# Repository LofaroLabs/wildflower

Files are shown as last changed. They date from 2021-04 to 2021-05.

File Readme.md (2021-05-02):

<!DOCTYPE HTML>
<html lang="en-US">
  <head>
    <meta charset="UTF-8">
  </head>
  <body>
    <!--Main Header-->
    <h1> Project Wildflower UAS </h1>
    <!--Logos-->
    <p float="left">
      Lofaro Labs Logo
      Project Wildflower Logo
    </p>
    <!--Link Bar-->
    <div id="NavBar">
      <p>  
        <a href="#Introduction" target="_blank">Approach</a>
         | 
        <a href="#PCBAndPowerSystems" target="_blank">PCB & Power Systems</a>
         | 
        <a href="#SoftwareAndPsuedocode">Software & Psuedocode</a>
         | 
        <a href="#BriefHistoryofArduino">Brief History of Arduino</a>
         | 
        <a href="#SensorsAndMotorDrivers">Sensors & Motor Drivers</a>
         | 
        <a href="#Results">Results</a>
         | 
        <a href="#Conclusion">Conclusion</a>
         | 
        <a href="#References">References</a>
         | 
        <a href="#ProjectPresentation">Project Presentation</a>
         | 
        <a href="https://www.youtube.com/watch?v=GgbFuCZchfk" target="_blank">Project Presentation on YouTube</a>
         | 
        <a href="http://lofarolabs.com/" target="_blank">Lofaro Labs Website</a>
    </div>
    <!--Section 0: Abstract-->
    <div>
      <p> 
        &nbsp;&nbsp;&nbsp;&nbsp;Since the turn of the millennium, unmanned aerial vehicles (UAVs) have gone from being used for highly specialized applications to becoming one of the primary approaches to mission success within the defense sector. UAVs are unmatched in terms of mission success versus collateral damage - and as production costs continue to rapidly fall, it is only natural that UAVs will continue to become a more common tool of militaries around the world. One of the most recent developments in the world of UAVs has been the growing consumer market for ultralight unmanned aerial systems (UAS). Some commercial products have demonstrated the viability and flexibility of inexpensive, open source, ultralight UAS systems. Unfortunately, most consumer products on the market cannot be approved for high security applications due to the inherent security risks posed by foreign-manufactured products. Therefore, the defense industry has need of an American-made ultralight UAS if it wants to pursue the potential applications that this technology allows. 
      </p>
      <p>
        &nbsp;&nbsp;&nbsp;&nbsp;This paper entails the results of our research and development work over the past 9 months. We are proud to present the results of our testing on a brushed-motor, unmanned aerial system (UAS) quadcopter designed in preparation of developing a brushless quadcopter in the future. Beginning in September of 2020, we began to perform research on designing a lightweight quadcopter out of a single printed circuit board (PCB) in order to meet the need for a quality, domestically produced UAS. Today, a great number of quadcopters are produced in foreign countries or with foreign programmed components. While many of these common quadcopters have demonstrated the general usefulness and cost-efficiency of their use, their foreign origins make them unusable by the federal government and military sectors due to concerns over information safety. Data concerning their activities is often sent to and kept on insecure servers[CNN and OSTI.gov, second not quoted], and can provide easy access points for malicious entities to otherwise secure systems when allowed to connect[Avast]. 
      </p>
      <p>
        &nbsp;&nbsp;&nbsp;&nbsp; As a result, our project was designed to fill this gap by providing a secure, American made UAS capable of remote operations. This paper covers the design process, creation, and testing of our quadcopter over the past two semesters. Our section on the PCB & Power System Design describes the design choices we made in structuring our board, as well as our choice of using a dual power system to power the motors and microcontroller separately. The Software & Pseudocode section goes over the general flow of our real time system, and is followed by a Brief History of Arduino. Sensors and Motor Drivers describe the input and output devices we thought best fitting for our UAS. The control systems elaborates further on our real time system. Finally, the Unit Testing and Results slide show the results of our research as we make the Wildflower hover and tilt at will, bringing us to our conclusion.
      </p>
      <hr>
    </div>
    <!--Section 1: Introduction-->
    <div id="Introduction">
      <h1>Approach</h1>
      <h3>The Problem</h3>
      <p> 
        &nbsp;&nbsp;&nbsp;&nbsp;The idea for the Wildflower arose from the desire for an American designed and programmed quadcopter in a market saturated with foreign-made quadcopters. The need for American Unmanned Aerial Systems (UAS) has been apparent for several years. In August 2017, “the Army banned the use of DJI drones citing ‘cyber vulnerabilities’” [1,2]. In May 2018, the DoD followed suit, banning not only the purchase of DJI drones, but the purchase of all commercial off-the-shelf (COTS) drones” [3,4]. Shortly after, several alarming vulnerabilities were discovered involving the DJI Go Phone application [5]. Such vulnerabilities included “access to facial recognition data (even when the system was off)” [5]. It’s not a far stretch to assume that the ban on government funding for blacklisted drones may soon extend to universities that receive government grants.
      </p>
      <p>
        &nbsp;&nbsp;&nbsp;&nbsp;The COTS ban, while seemingly necessary, has left a lot of government employees and contractors with a job to do without the tools to do it. There have never been many US-made drones available on the market, but the pool of eligible candidates dwindles further when the drones containing foreign software are excluded. While there currently exists a number of American based alternatives for remote controlled unmanned aerial systems, such systems often cannot be used out-of-the-box for important security or government related tasks. For example, many of these UASs are not easily configurable, having been made for the general public to enjoy. Additionally, the communications methods for these systems might not be securable, posing a risk of malicious infiltration into crucial US government and military organizations. 
      </p>
      <h3>The Solution</h3>
      <p>
        &nbsp;&nbsp;&nbsp;&nbsp; Dr. Lofaro’s initial idea for the Wildflower was conceived as a direct result of his inability to use certain UAS’s for his work at the Naval Research Lab. Our project aims to fill this gap by providing a trustworthy and easily modifiable aerial system designed in a way that allows easy debugging and testing for those who use it. We make use of a VL6180x short-range light detection and ranging (LIDAR) sensor, a VL53L0x long-range LIDAR sensor, and a BNO055 inertial measurement unit (IMU) sensor to feed all of the information we need to our Adafruit Feather M0 microcontroller (MCU) with embedded ATWINC1500 Wifi chip, in order to keep it airborne and mobile. We communicate commands to the Feather over wi-fi and through a ground station that can be easily installed on a user’s computer, allowing for increased portability and relatively straightforward setup and teardown when moving from one area of use to another or starting to use it for the first time. 
      </p>
      <hr>
    </div>
    <!--Section 2: PCB & Power Systems-->
    <div id="PCBAndPowerSystems">
      <h1>PCB & Power Systems</h1>
      <div>
        <p> 
          &nbsp;&nbsp;&nbsp;&nbsp;The circuit board for the UAS design consists of a 51x51mm body with four 10mm arms connected to circular motor mounting points which are 19mm in diameter. The motors and rotors are mounted on the outer circle of the PCB connected to the quadrotor’s arms, while some of the heavier electronics are placed towards the center of the PCB for stability. 
        </p>
        <!--PCB-->
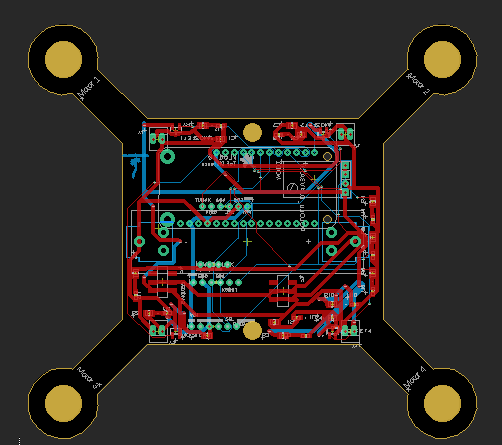
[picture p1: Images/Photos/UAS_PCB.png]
Final PCB
        
        <!--Schematic-->
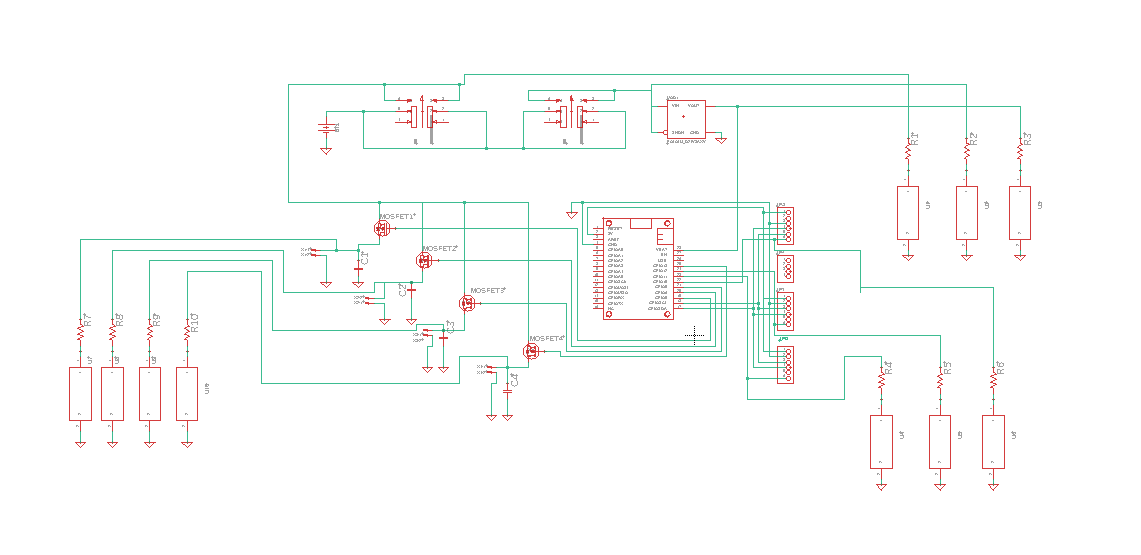
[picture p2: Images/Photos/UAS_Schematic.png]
Final Schematic
        
        <p>
          &nbsp;&nbsp;&nbsp;&nbsp;The UAS PCB circuitry consists of a battery to supply power to the circuit. Two switches are applied in parallel with the battery to function as on/off switches to the motors and the microcontroller respectively. From the on/off switch, power is supplied to the microcontroller through a 3.3V voltage regulator at 300milliamperes. This voltage regulator was chosen since the recommended voltage input to the Feather is 3 to 5 volts and the recommended current that is input to the Feather is 250 milliamperes to 400 milliamperes. The microcontroller then uses the 3.3-volt output pin to supply power to the close-range lidar sensor, the long-range lidar sensor, and the inertial measurement unit (IMU).  Power is supplied to the motors using a single metal-oxide-semiconductor field-effect transistor (MOSFET), rather than using an H-bridge circuit for simplicity. The power supplied from the battery is supplied to the drain terminal of the MOSFET and the source MOSFET is connected to the motors. The amount of power supplied to the motors is manipulated by pulse-width modulation of the gate terminal of the MOSFET. When applying a signal from the Feather to the MOSFET with a high duty cycle, the drain current will increase; however, the opposite will occur when the input signal has a low duty cycle. The drain current of a MOSFET acting in the saturation region can be calculated by the following equation:
        </p>
        <!--Drain Current Equation-->
        Drain Current Equation for MOSFET in the triode region
        <p>
          &nbsp;&nbsp;&nbsp;&nbsp;The transconductance parameter is the portion of this equation that dictates the amount of drain current based on the input voltage; thus, choosing a MOSFET with the correct transconductance parameter was critical. Another critical criterion that had to be met was having a low threshold voltage. With a low threshold voltage, the triode region of the MOSFET is entered with a low gate to source voltage. Since the gate to source voltage will at most be equivalent to the drain to source voltage in our case, the closest that our MOSFET will act to the triode region Is on the bound of the triode and saturation regions. For all of these reasons, we have chosen to use the SI2342DS. Shown below, this model of MOSFET will allow a large drain current to pass through MOSFET from the battery to the motor when a large gate voltage is applied; however, the opposite will occur when the gate to source voltage is lower than or equal to the threshold voltage. 
        </p>
        <!--Image of the FET graph-->
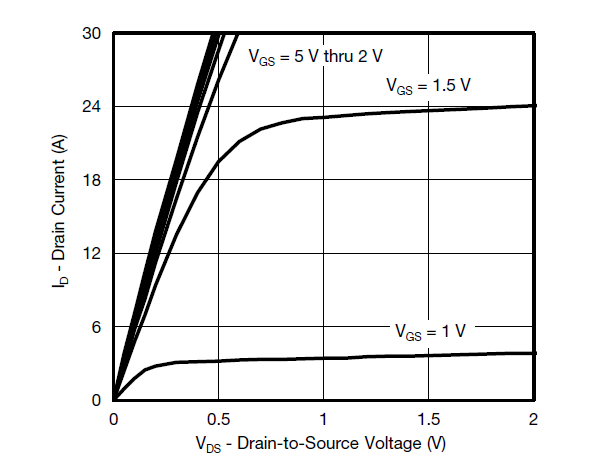
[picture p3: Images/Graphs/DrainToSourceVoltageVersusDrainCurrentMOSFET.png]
MOSFET Drain to Source Voltage Versus Drain Current
        
        <p>
          &nbsp;&nbsp;&nbsp;&nbsp;Finally, the node connected to the motor inputs is also connected to a decoupling capacitor. This capacitor will cancel out some of the impedance caused by the inductive load of the motor as well as filter out any high frequency signal components. 
        </p>
        <hr>
      </div>
    </div>
    <!--Section 3: Software and Psuedocode-->
    <div id="SoftwareAndPsuedocode">
      <h1>Software & Psuedocode</h1>
      <div>
        <p> 
          &nbsp;&nbsp;&nbsp;&nbsp;The Adafruit Feather M0 microcontroller uses the on-board RF module, the ATWINC1500, to communicate with the ground station over a 2.4 gigahertz WiFi network. The Feather communicates with the on-board ATWINC1500 module using serial peripheral interface (SPI) communication. The RF module then connects to the same WiFi network to which the ground station is connected. The communication between the microcontroller and the ground station is done by transmitting packets using User Datagram Protocol (UDP). UDP was chosen over Transmission Control Protocol (TCP) since UDP is a faster communication method. This is due to UDP being a connectionless protocol; thus, the setup and retransmission times of UDP are much quicker than that of TCP. The tradeoff of that UDP is more error prone since it does not use include sequencing numbers. Since we are not transmitting large files, any transmission error is accounted for by built-in selective repeat ARQ (Automatic Repeat Request).  The UDP packets are sent from the ground station to the microcontroller on port 2390 and packets received from the microcontroller are obtained from port 3000. 
        </p>
        <!--Place Communications Diagram-->
        
        <!--Place GUI-->
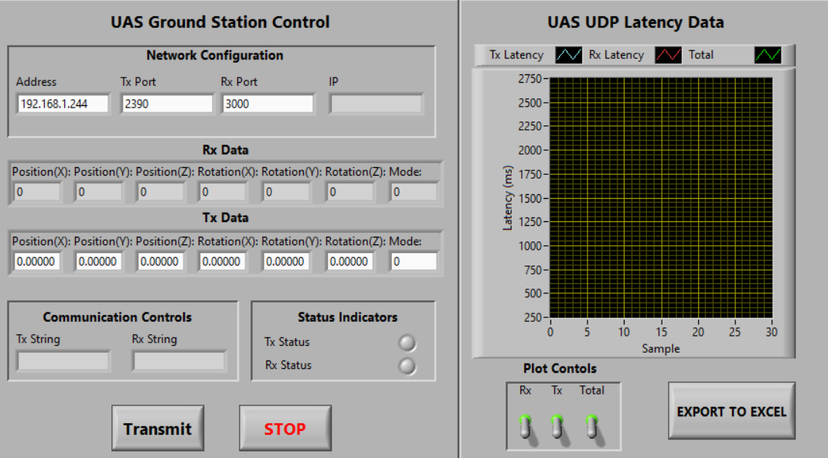
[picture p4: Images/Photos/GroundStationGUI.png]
Ground Station GUI
        
        <p>
          &nbsp;&nbsp;&nbsp;&nbsp;The data being transmitted is in the format of a strings. Functions on the host and client side are implemented to format and parse strings to and from data structures. When the data is received by the microcontroller in the correct format, another string is transmitted, which serves as format-based Stop-and-wait ARQ. If the acknowledgment is not received by the ground station, the packet is then retransmitted until reaching a timeout value. The combination of this software implementation of format-based Stop-and-Wait ARQ, the built-in Selective Repeat ARQ of UDP, and the small data quantity serve as an error-limiting provide more reliable transmission while still maintaining high transfer rates. 
        </p>
        <!--Software Flow Chart-->
        Software Flowchart
        <!--UML Diagram-->
        UML Diagram
        <hr>
      </div>
    </div>
    <!--Section 4: Brief History of Arduino-->
    <div id="BriefHistoryofArduino">
      <h1>Brief History of Arduino</h1>
      <div>
        <p> 
          &nbsp;&nbsp;&nbsp;&nbsp;Arduino, as it is known today, is a forked version of an open-source programming project called Wiring. Wiring was started in 2003 by grad student Hernando Barragán for his Master's thesis at the Interaction Design Institute in Ivrea. His idea was to create "a microcontroller-based hardware controller platform that was simple enough to program that it could be used by artists"[6] without needing to know the specific programming syntax for the board that said code was running on. This enables users to implement the same code (with some minor tweaking to pin numbers) to run a program on a variety of boards. So, we designd our code to be Arduino compliant, without any bit banging or direct processor level interaction, so that it can be easily modified by the average user and so it can go on any microcontroller. 
        </p>
        <hr>
      </div>
    </div>
    <!--Section 5: Sensors & Motor Drivers-->
    <div id="SensorsAndMotorDrivers">
      <h1>Sensors & Motor Drivers</h1>
      <div>
        <p> 
          &nbsp;&nbsp;&nbsp;&nbsp;Onboard sensors are used to maintain a specific angle. The BNO055 IMU not only keeps track of our angle relative to the start-up orientation, but it also is able to determine angular velocity and linear acceleration of the Wildflower whenever we need it. Said orientation, velocity, and acceleration inputs are fed into our PID so that it can adjust the motors spin speed to reach the desired orientation of our UAS. We adjust the desired orientation via UDP communications with our ground station. 
        </p>
        <p>
          &nbsp;&nbsp;&nbsp;&nbsp;The Wildflower makes use of three different sensors to help keep it in a user-specified location and orientation. The first is the BNO055 inertial measurement unit, which is capable of tracking the UAS’s absolute orientation, angular velocity, and linear acceleration, of which we need in order to make our PID controller work. The absolute orientation provides the provides the proportional section of our PID formula, representing the base difference that our UAS needs to rotate in order to meet the desired orientation. The velocity is used in part of the derivative contribution to the formula so we can see the rate at which it’s rotating about an axis and increase or decrease the rotational force being applied in order to reach that point in a timely manner while minimizing overshoot. The recordings of both can be stored onboard and used with some averaging to give us the integrational part of our formula. This completes our PID function, giving us the appropriate forces, we need to apply on each axis to reach our goal. Said forces are then fed into a function which converts them into values which tell the motors at what rate they should spin in order to best achieve the desired state. 
        </p>
        <!--Peripheral Circuit-->
        Peripheral Circuitry
        <p>
          &nbsp;&nbsp;&nbsp;&nbsp;The other two sensors are LIDARs specified to work at different ranges, with one being our long range one and the other being our close range one. The long one is rated for a range of 50 mm to 1200 mm, allowing us to determine how high off the ground we have ascended (our altitude) to a degree. Its primary purpose is helping the Wildflower maintain a specified height. The second one has an effective range of 5 mm to 100 mm, which aids in landing to ensure that we don’t drop too quickly. 
        </p>
        <hr>
      </div>
    </div>
    <!--Section 6: Results-->
    <div id="Results">
      <h1>Results</h1>
      <div>
        <p> 
          &nbsp;&nbsp;&nbsp;&nbsp;The first unit test we performed was a single motor thrust measurement. After the move from the brushless DC motors to the brushed DC motors was made, it was important to establish a new thrust capability threshold for the new motors. To accomplish this, a single motor was mounted in putty to a kitchen scale. The motor was hooked up to a desktop power supply and the propeller was switched in order to have the motor trust against the scale. Voltage was ramped up until the maximum output of the battery was reached resulting in a maximum of 18 grams of thrust. This gave the final four motor drone a potential 72 grams of maximum thrust. 
        </p>
        <!--Single Motor Testing Image-->
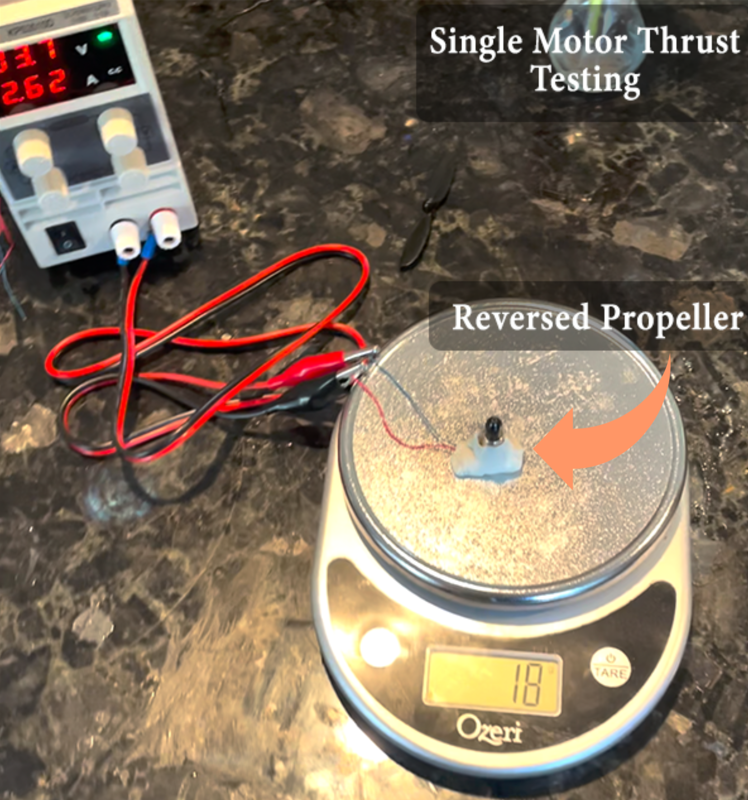
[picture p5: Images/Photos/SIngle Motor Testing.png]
Single Motor Testing Image
        
        <!--Single Motor Test Video-->
        Single Motor Test Video
        <p>
          &nbsp;&nbsp;&nbsp;&nbsp;After the drone had been fully assembled and all the sensors individually tested, a full drone thrust test was performed. The first interaction of this test involved mounting the drone in its normal flying position to a kitchen scale using a mount secured to the base of the drone. This test resulted in false readings as the propeller wash interfered with the scales measurements and needed to be reperformed. The second test involved inverting the drone and attaching it to an even higher secure mount. The inverted position significantly reduced propeller wash intensity and the higher mount ensured plenty of clearance between the drone and the scale. This resulted in a successful measurement of full drone thrust at 68 grams. The loss of thrust power between the single motor test and the full drone test is was due to the introduction of the motor arms to the air column of the propellers. This resulted in a 5% loss of thrust per motor.  
        </p>
        <!--All Motor Testing Image-->
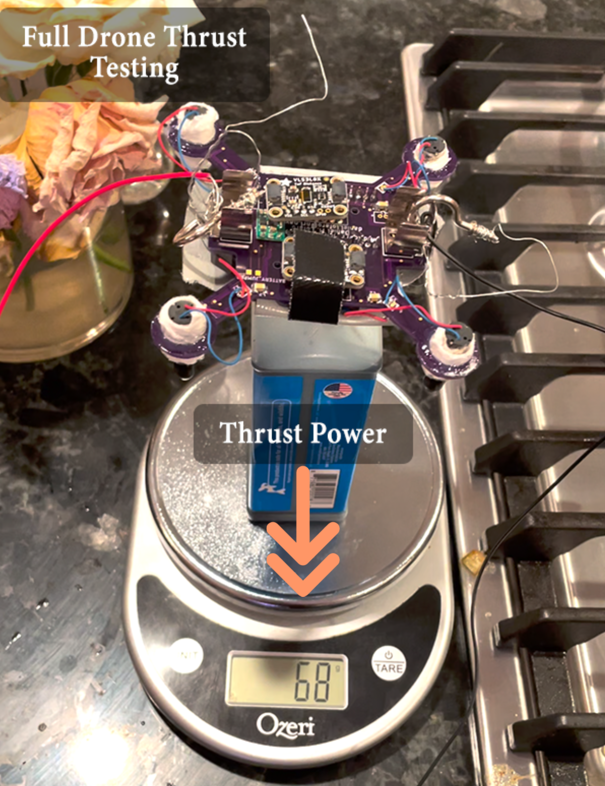
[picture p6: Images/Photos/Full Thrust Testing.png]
All Motor Thrust Test
         
        <!--All Motor Testing Video-->
        Full Thrust Test Video
        <p>
          &nbsp;&nbsp;&nbsp;&nbsp;After establishing our maximum thrust, our average flight time could be determined based on power draw from the stationary hovering drone. This was determined to be 8.73A in total current draw at 3.7V. Given that our battery has a max charge of 2.6Ah and that the battery will drop below the required output voltage at 20% charge, we determined that an average flight time of 14 minutes would be achievable.  
        </p>
        <!--Flight Time Testing-->
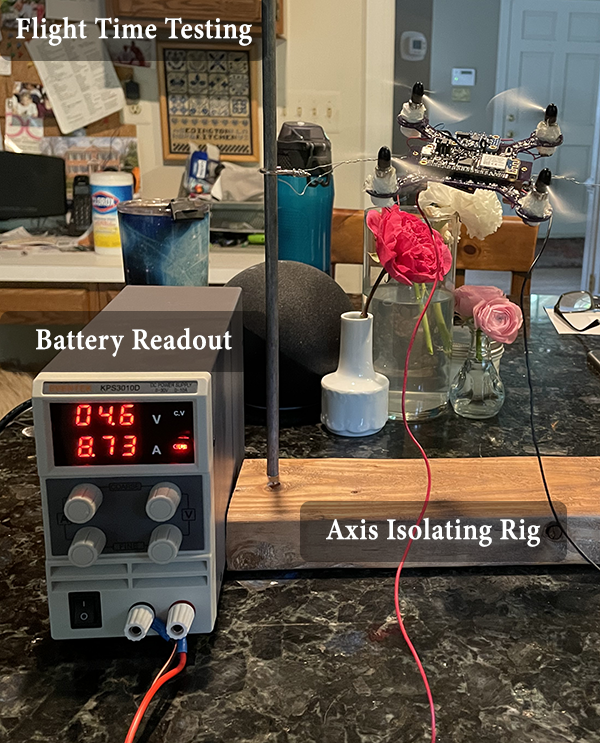
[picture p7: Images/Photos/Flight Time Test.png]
Flight Time Testing Image
        
        <!--Show Video of Generic Flight-->
        Flight Video
        <p>
          &nbsp;&nbsp;&nbsp;&nbsp;Approaching the initial hover test came with a few hurdles. Although we were sure we could get the blades to spin, we did not have a sufficient rig to ensure the drone’s movement would be isolated to the z-axis. A rig was constructed using spare lumber and two steel rods to act as stationary mounts. Hooked around the mounts were two lightweight hanging screws threaded with wire. The wire was then attached to the drone and third rod was added to ensure only a single degree of motion would be achievable. With the rod created and the drone placed in it, the battery terminals were connected to a desktop power supply in order to not waste batteries for the tests.  
        </p>
        <!--Hover Testing Videos-->
        Free Hover Video
        Hover Testing
        <p>
          &nbsp;&nbsp;&nbsp;&nbsp;The initial hover test was conducted with the power being directly fed into the motor system, fully bypassing the control hardware. This initial test was a structural one to ensure basic flight could be achieved as well as a stress test for the design overall and the motor mounts. This initial test showed that at the battery's max voltage, the original motor mount design failed catastrophically. Approximately three seconds after flight was achieved one of the motors was violently wrested from its mount. This resulted in a redesign of the motor mounts to ensure proper hover. The reworked motor mounts were tested a second time using the single dimension rig. This second test resulted in successful takeoff and flight maintenance. Although altitude was not actively controlled, it was limited by the cables connecting the drone to the desktop power supply.  As the voltage to the drone was slowly lowered, it successfully made a gentle landing on the rig, showing that the motors do not sudden cut out at the drone had the ability to safety land from altitude.  
        </p>
        <!--Takeoff and landing test-->
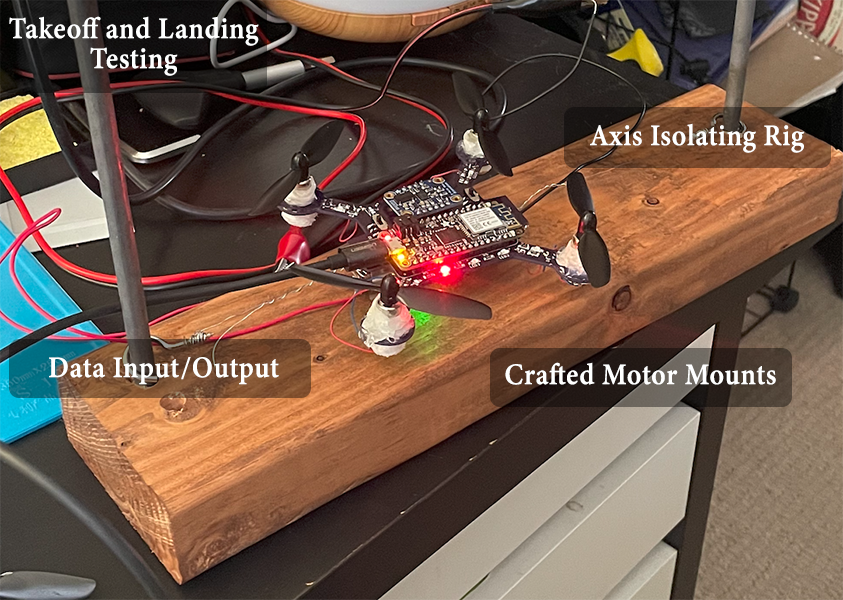
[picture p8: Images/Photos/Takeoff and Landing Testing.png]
Takeoff and Landing test
        
        <!--Takeoff and Landing Video-->
        Takeoff and Landing Test
         <p>
          &nbsp;&nbsp;&nbsp;&nbsp;The first altitude control test involved the same test rig setup but this time the full sensor package was powered, and the control system was installed. There was a delay in initial takeoff as the spin up process took a bit longer than anticipated. Ultimately it took 1.7 seconds for the prototype to reach an altitude of 400m from a cold start. During the flight the climb rate of the drone adjusted during the sensor overlap between our short- and long-range LIDARs. This sensor overlap meant that as it approached the final altitude, the sensor differences resulted in a delay in actually reaching the desired altitude.  
        </p>
        <!--Takeoff Time to 400mm graph-->
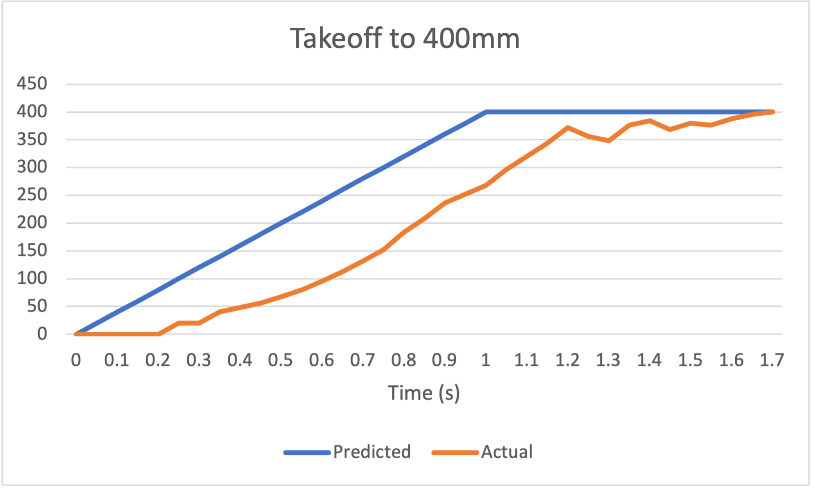
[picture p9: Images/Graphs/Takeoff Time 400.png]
Takeoff Time Graph
        
        <!--Takeoff Video-->
        Takeoff Video
        <p>
          &nbsp;&nbsp;&nbsp;&nbsp; Once it was established that the drone could successfully takeoff, a unit step altitude test was performed. This involved establishing stable flight at an altitude of 50mm and then adjusting the setting to a new height of 70mm. In the execution of this maneuver, the drone initially lost altitude before beginning to climb due to a temporary loss of synchronization between motors. The unit then overshot the desired altitude and took three cycles before it could finally correct to the desired altitude.  
        </p>
        <!--Unit Step Graph-->
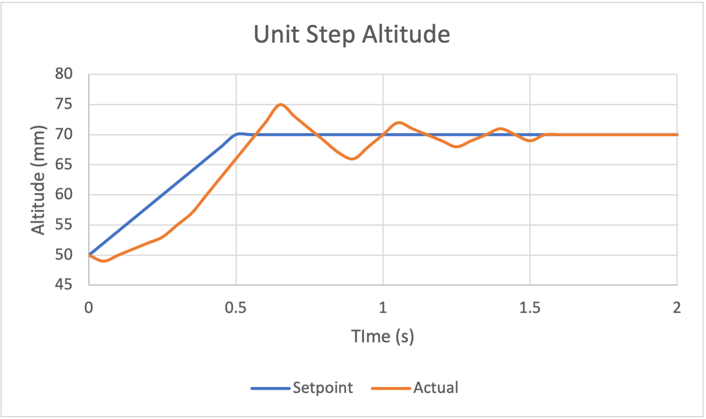
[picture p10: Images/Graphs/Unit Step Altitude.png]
Unit Step Graph
        
        <p>
          &nbsp;&nbsp;&nbsp;&nbsp;Testing continued with single axis motion testing. This was important to establish independent axis control by the programming and hardware. By placing the unit in the single axis test unit and having it store small data runs on the onboard memory, data was captured on stabilization following an outside force applied to the hovering drone. The unit was rocked in the roll position and the roll angle was captured for 5 seconds. In this time after the initial velocity of the force wore off, the resonance in the test rig wiring interfered with the drone. But after that too wore off the drone successfully entered system resonance. Although this means that it was never perfectly still, it did show that with gain adjustments in the PID program that resonance should be able to be eliminated.  
        </p>
        <!--Single Axis Motion Testing-->
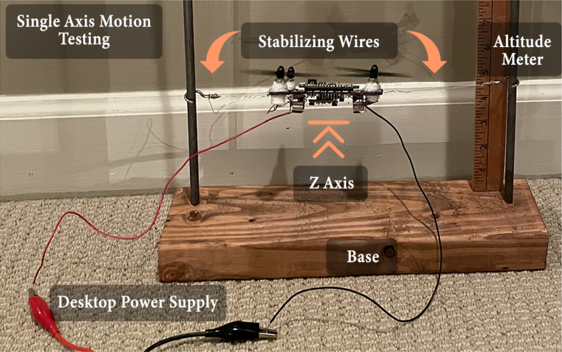
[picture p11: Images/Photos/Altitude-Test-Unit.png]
Single Axis Motion Testing Setup
        
        <!--Roll Angle Recovery Graph-->
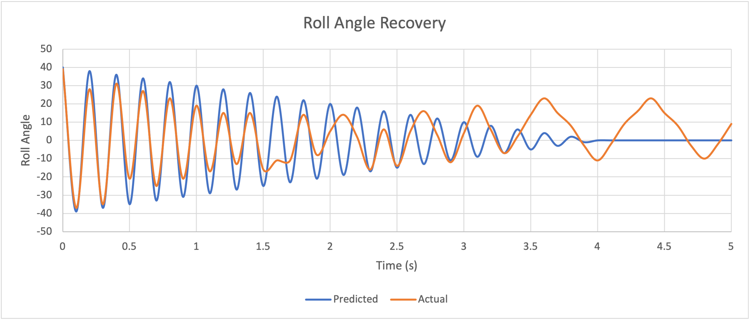
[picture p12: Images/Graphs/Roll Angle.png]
Roll Angle Graph
        
        <!--Roll Test Video-->
        Roll Test Video
        <p>
          &nbsp;&nbsp;&nbsp;&nbsp;  The communication system of our UAS introduces latency within the system; thus, a unit test for communication latency must be performed to determine appropriate data refresh rates from our ground control station and our UAS module. The latency test was performed for an entire data refresh cycle. This cycle consists multiple actions. The first of these actions is an initial transmit of data from the ground station to the UAS. This transmit then waits for an acknowledgement. If the acknowledgement is not received, a timeout value is reached and the cycle progresses. If an acknowledgment is received, then the cycle will progress. The next portion of the information exchange cycle is where the data read from the UAS’s onboard sensors is transmitted the ground station, which listens on the specified port for incoming datagram packets.  This data is then received in string format, parsed, and placed within data structures.  
        </p>
        <p>
          &nbsp;&nbsp;&nbsp;&nbsp;The entire cycles latency was measured from the ground station by measuring the system time at the beginning of the first stage of our data communication cycle and at the end of the data communication cycle. These two measured system times were subtracted to find the difference in milliseconds. After running 102 data communication samples, the data was exported to an Excel file. The graph and data analytics demonstrated below were generated within Microsoft Excel. 
        </p>
        <!--Latency Graph-->
        Latency Test Graph
        <p>
          &nbsp;&nbsp;&nbsp;&nbsp; The average transmit-receive latency was 540.245 milliseconds. Since User Datagram Protocol has limited error checking, the communication speeds are highly variable. This is apparent on the graph, which shows that most of the transmissions required around 255 milliseconds; however, due to the outliers, the average was increased to double that. The standard deviation is 512.995 milliseconds, which shows that based on a normalized Gaussian distribution, the 68.2% of our data lies within the one an interval of 512.995 milliseconds from our mean latency of 540.245 milliseconds.  
        </p>
        <p>
          &nbsp;&nbsp;&nbsp;&nbsp; The main benefactors of our project would most likely be those who require unmanned aerial systems for security applications (such as the United States government or private security industry,) or anyone who wants an unmanned aerial system designed with transparency in mind. Creating a successful product could inspire other engineers to design more domestically based aerial systems, resulting in more quality products of domestic origin. 
        </p>
        <p>
          &nbsp;&nbsp;&nbsp;&nbsp; The Wildflower has great potential for use inside the government sector, particularly because of the need for secure and domestic UAVs if the government wishes to use them at all. However, the future researchers will implement other functionalities on the Wildflower, allowing it to be used in a wide array of applications through attachable modules.. 
        </p>
        <p>
          &nbsp;&nbsp;&nbsp;&nbsp; The final design will have some form of replaceable arms with designated break points
        </p>
        <p>
          &nbsp;&nbsp;&nbsp;&nbsp; The Project Wildflower UAS is currently a PCB that can hover and maintain stability amongst a single axis. The PCB and brushed DC motor circuitry have been completed and we are able to communicate with the UAS through UDP over WiFi. The information sent from the ground station to the UAS serves as control information for the UAS, while the return data to the ground station serves as data from the sensors. Altogether, the communication system is fully functional. The UAS’s onboard sensors are also functioning entirely. The microcontroller can communicate with the sensors via I2C protocol. The data is then stored on the microcontroller in a data structure. Research and prototype boards have also been designed for further development with brushless DC motors in the future.  
        </p>
        <hr>
      </div>
    </div>
    <!--Section 7: Conclusion-->
    <div id="Conclusion">
      <h1>Conclusion</h1>
      <div>
        <p> 
          &nbsp;&nbsp;&nbsp;&nbsp;This course provided our team with an incredible opportunity to learn about the many facets of designing and building an electrical engineering project. Starting out, there was not a single person on our entire team who knew how to do more than one or two of the skills out of the many that this project required. Dr. Lofaro was an incredible mentor throughout our entire learning process, sometimes devoting an entire hour of our weekly meetings to explaining a concept. We have developed many skills and methods during the course of this senior design project that we will be able to apply to our careers and even our personal lives. 
        </p>
        <p>
          &nbsp;&nbsp;&nbsp;&nbsp;First, we learned an incredible amount about PCB design. Prior to this semester, none of us had really done much in the way of designing circuits on a PCB. The few of us that had had done so as part of a course that they had taken in the EE program. Throughout the semester, several of our team members developed and honed their skills through prototype development. Our team made four BLDC boards and three brushed DC boards. 
        </p>
        <p>
          &nbsp;&nbsp;&nbsp;&nbsp;The first few boards that we developed were really rough. We made a lot of design mistakes, things were not organized, and we left empty spaces on a board that was meant to be as tiny as possible in order to reduce the gross weight of the drone. Our biggest mistake in maximizing the “real estate” of the board was in using the Auto-Routing tool in EagleCAD, which made more of a mess than we ever could have made by hand. That was an important lesson to learn about apparent ease of use versus knowing how to do things manually. As we continued on, our board prototypes got better and better. We moved on from boards which could operate one BLDC motor to boards that could operate all four BLDCs. When we decided that we needed to switch away from BLDC motors and instead use brushed DC motors, we had already developed the PCB layout skills necessary to produce those brushed boards incredibly easily. 
        </p>
        <p>
          &nbsp;&nbsp;&nbsp;&nbsp;Our team also learned about the Agile Iterative Process and the V-Model Unit Testing Process. At the start of the semester, none of us had ever heard of either of these processes. By the end of the semester, we are well versed in their applications. This is important because some workplaces operate using the Agile Iterative Process, so knowing how it works would give our group members an advantage applying to such organizations. The Agile Iterative Process also taught us about keeping up on our tasks. Although one of the main benefits of Agile is that multiple tasks can be completed in parallel, we did not have the luxury of slacking off due to the ECE492/3 project backlog. Since we already knew what we had to start and when we had to start it, we were all kept accountable for any missed work that would impede the progress of future iterations of the project. 
        </p>
        <hr>
      </div>
    </div>
    <!--Section 8: References-->
    <div id="References">
      <h1>References</h1>
      <div>
        <p> 
          [1] “How U.S. agencies’ trust in untested software opened the door to hackers - POLITICO.” <a href="https://www.politico.com/news/2020/12/19/how-federal-hack-happened-448602">https://www.politico.com/news/2020/12/19/how-federal-hack-happened-448602</a> (<em>accessed Apr. 29, 2021</em>). 
        </p>
        <p>
          [2] S. H. Stone Mike, “U.S. Justice Department seeks to curb risks of foreign-made drones,” <em>Reuters</em>, Oct. 08, 2020. 
        </p>
        <p>
          [3] J. Daniels, “US Army reportedly bans Chinese-made drone, citing ‘cyber vulnerabilities,’” CNBC, Aug. 04, 2017.<a href="https://www.cnbc.com/2017/08/04/us-army-bans-chinese-made-drone-citing-cyber-vulnerabilities.html"> https://www.cnbc.com/2017/08/04/us-army-bans-chinese-made-drone-citing-cyber-vulnerabilities.html </a> (<em>accessed Apr. 30, 2021</em>). 
        </p>
        <p>
          [4] “Statement Regarding Commercial Drones Security Issues | Research and Creative Activity | NDSU.” <a href="https://www.ndsu.edu/research/for_researchers/unmanned_aircraft_systems/statement_regarding_commercial_drones_security_issues/">https://www.ndsu.edu/research/for_researchers/unmanned_aircraft_systems/statement_regarding_commercial_drones_security_issues/ </a> (<em>accessed Apr. 22, 2021</em>). 
        </p>
        <p>
          [5] M. McNabb, “No Department of Justice Funds for DJI Drones: DOJ Makes the Ban Official, but Some Federal Agencies May Suffer,” DRONELIFE, Oct. 09, 2020. <a href="https://dronelife.com/2020/10/09/no-federal-funds-for-dji-drones-doj-makes-the-ban-official-but-some-federal-agencies-may-suffer/">https://dronelife.com/2020/10/09/no-federal-funds-for-dji-drones-doj-makes-the-ban-official-but-some-federal-agencies-may-suffer/ </a>(<em>accessed Apr. 30, 2021</em>). 
        </p>
        <hr>
      </div>
    </div>
    <!--Project Presentation-->
    <div id="ProjectPresentation">
      <h1> Our Project Presentation</h1>
      <h3>QR Code to Project Wildflower Presentation on YouTube</h3>
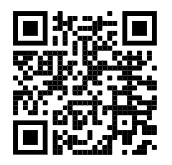
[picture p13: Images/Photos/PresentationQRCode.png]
YouTube Presentation QR Code
      
      <ul>
        <li><a href="https://github.com/LofaroLabs/wildflower/blob/master/Videos/Video%20Files/Project%20Wildflower%20Presentation.mp4" target="_blank">Project Wildflower Presentation (GitHub)</a></li>
        <li><a href="https://www.youtube.com/watch?v=GgbFuCZchfk" target="_blank">Project Wildflower Presentation (YouTube)</a></li>
      </ul>    
    </div>
    <hr>
    <!--Copyright Information-->
    <footer> <small>&copy; Copyright 2021, Lofaro Labs</small> </footer>
    </body>
</html>

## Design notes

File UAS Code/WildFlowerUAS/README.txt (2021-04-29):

1. PLACE FILE IN LIBRARIES FOLDER FOR ARDUINO
	-If on Windows 10, the folder should be at "C:\Users\Username\Documents\Arduino\libraries\".

2. CLASSES TO CALL and PUBLIC METHODS 
	SENSORS
		SENSORS(void);
			-Creates a class instance.
		void Initialize(void)	
			-Initializes the sensors to be able to read data.
		void ReadIMU(void)
			-Reads data from IMU and stores it into global variables.
		void ReadCloseRangeLIDAR(void)
			-Reads data from the close-range LIDAR and stores it in a global variable.
		void ReadLongRangeLIDAR(void)
			-Reads data from the long-range LIDAR and stores it in a global variable.
	UAS_WiFi
		UAS_WiFi(void);
			-Creates a class instance 
		void Initialize(const char ssid[], const char pass[], unsigned int localPort);
			-Initializes WiFi connections, prints the status, and begins listening on the specified port for packets transmitted through UDP.
		void Send(const char message[], unsigned int port);
			-Sends the message through UDP on the specified port. 
		void Receive(void);
			-Listens to specified port in Initialize for commands transmitted from the ground station.

3. IMPORTANT GLOBAL VARIABLES 
	I2C Addressing
		-VL6180X_ADR
			-Long-Range LIDAR address set to 0x29.
		-VL53L0X_ADR
			-Close-Range LIDAR address set to 0x30.
		-BNO055_ADR 
			-IMU adress set to 0x28.
	Sensor XSHUT Pins 
		-VL6180X_XSHUT
			-XSHUT pin for Long-Range LIDAR, which is 11.
		-BNO055_XSHUT
			-XSHUT pin for IMU, which is 10.

	IMU Data
		-TxData
			-Structure with a 3D vector for Orientation and Rotation, and an unsigned 16-bit integet to enumerate mode selection
				-Note: This structure is the same type as the Ground Station Command Data
	Long-Range and Close-Range LIDAR Return Data
		-Lidar
			-Structure consisting of the Close-Range proximity in millimeters, the Long-Range proximity in millimeters, and the Close-Range LIDAR's LUX.
	Ground Station Commands
		-RxData
			-Structure with a 3D vector for Orientation and Rotation, and an unsigned 16-bit integet to enumerate mode selection
				-Note: This structure is the same type as the IMU Data

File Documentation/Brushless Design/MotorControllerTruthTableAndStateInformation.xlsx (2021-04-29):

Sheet: Truth Table
Sum: | GPIO 1 | GPIO 2 | GPIO 3 | GPIO 4 | GPIO 5 | GPIO 6 | A | B | C | State:
0 | 0 | 0 | 0 | 0 | 0 | 0 | HIGH Z | HIGH Z | HIGH Z | N/A
1 | 0 | 0 | 0 | 0 | 0 | 1 | HIGH Z | HIGH Z | 0 | N/A
2 | 0 | 0 | 0 | 0 | 1 | 0 | HIGH Z | HIGH Z | 1 | N/A
3 | 0 | 0 | 0 | 0 | 1 | 1 | HIGH Z | HIGH Z | N/A | N/A
4 | 0 | 0 | 0 | 1 | 0 | 0 | HIGH Z | 0 | HIGH Z | N/A
5 | 0 | 0 | 0 | 1 | 0 | 1 | HIGH Z | 0 | 0 | N/A
6 | 0 | 0 | 0 | 1 | 1 | 0 | HIGH Z | 0 | 1 | N/A
7 | 0 | 0 | 0 | 1 | 1 | 1 | HIGH Z | 0 | N/A | N/A
8 | 0 | 0 | 1 | 0 | 0 | 0 | HIGH Z | 1 | HIGH Z | N/A
9 | 0 | 0 | 1 | 0 | 0 | 1 | HIGH Z | 1 | 0 | STATE 2
10 | 0 | 0 | 1 | 0 | 1 | 0 | HIGH Z | 1 | 1 | N/A
11 | 0 | 0 | 1 | 0 | 1 | 1 | HIGH Z | 1 | N/A | N/A
12 | 0 | 0 | 1 | 1 | 0 | 0 | HIGH Z | N/A | HIGH Z | N/A
13 | 0 | 0 | 1 | 1 | 0 | 1 | HIGH Z | N/A | 0 | N/A
14 | 0 | 0 | 1 | 1 | 1 | 0 | HIGH Z | N/A | 1 | N/A
15 | 0 | 0 | 1 | 1 | 1 | 1 | HIGH Z | N/A | N/A | N/A
16 | 0 | 1 | 0 | 0 | 0 | 0 | 0 | HIGH Z | HIGH Z | N/A
17 | 0 | 1 | 0 | 0 | 0 | 1 | 0 | HIGH Z | 0 | N/A
18 | 0 | 1 | 0 | 0 | 1 | 0 | 0 | HIGH Z | 1 | STATE 3
19 | 0 | 1 | 0 | 0 | 1 | 1 | 0 | HIGH Z | N/A | N/A
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

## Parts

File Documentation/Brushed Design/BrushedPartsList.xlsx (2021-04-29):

Component Name: | Part Number: | Vendor: | Quantity: | Unit Price: | Total Price: | Link: | Reasoning:
MICROCONTROLLER:
Adafruit Feather M0 | 3061 | Adafruit | 1 | $34.95 | $34.95 | https://www.adafruit.com/product/3061 | The microcontroller will be used to determine when power is supplied to the motors, as well as the for the interfacing to sensors, transmitting, receiving, and processing information
POWER:
Pololu 5V, 300mA Step-Down Voltage Regulator (D34V3F5) | 2098 | Pololu | 1 | $3.95 | $3.95 | https://www.pololu.com/product/2098 | The voltage regulator will be used between the power supplies in order to limit the power supplied to the microcontroller to avoid damaging this component.
Battery Clips | 36-54-ND | Digikey | 2 | $0.64 | $1.28 | https://www.digikey.com/en/products/detail/keystone-electronics/54/2254090 | The battery clips will be used to attach the batteries to the UAS for power.
18650 Battery (3500mAh) | N/A | Amazon | 1 | $19.49 | $19.49 | https://www.amazon.com/EBL-Rechargeable-Batteries-Flashlights-Headlamps/dp/B0874R85J2 | The battery will be used to supply power to the UAS.
Switch (JS202011SCQN) | 401-2002-1-ND | Digikey | 2 | $0.55 | $1.10 | https://www.digikey.com/en/products/detail/c-k/JS202011SCQN/2094299?s=N4IgTCBcDaIFIGUwAYUEY0IMIEUByIAugL5A | The switches will be used as on/off control both for the motor controller as well as the microcontroller.
SENSORS:
Adafruit BNO055 | 2472 | Adafruit | 1 | $34.95 | $34.95 | https://www.adafruit.com/product/2472 | This IMU will help us determine orientation, velocity, acceleration, etc. in order to maintain stabilty in the landing process
Adafruit VL6180X | 3316 | Adafruit | 1 | $13.95 | $13.95 | https://www.adafruit.com/product/3316 | This LIDAR sensor will be used on the bottom of the UAS for landing to determine when the UAS will be stopped.
Adafruit VL53L0X (STEMMA) | 3317 | Adafruit | 1 | $14.95 | $14.95 | https://www.adafruit.com/product/3317 | This LIDAR sensor will be used on the bottom of the UAS for landing to determine when the UAS will be stopped.
2.4GHz Mini Flex Antenna 100mm | 2308 | Adafruit | 1 | $2.50 | $2.50 | https://www.adafruit.com/product/2308 | This antenna will be used for the WiFi communications between the onboard WiFi chip integrated within the microcontroller and the ground station where the UAS is being controlled.
MOTORS:
N-Channel MOSFET (SI2342DS-T1-GE3) | SI2342DS-T1-GE3CT-ND | Digikey | 4 | $0.53 | $2.12 | https://www.digikey.com/en/products/detail/vishay-siliconix/SI2342DS-T1-GE3/4496221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 | The MOSFETs will be used to control when the motors receive power.
Motors | N/A | Amazon | 1 | $11.99 | $11.99 | https://www.amazon.com/Hobbypower-Coreless-53000rpm-8-5x20mm-Propeller/dp/B076M7G24G | The motors will be used to rotate propellers to generate thrust. This is how the unit will fly.
ETC:
100 Ohm Surface Mount Resistors (CR0805-FX-1000ELF) | CR0805-FX-1000ELFCT-ND | Digikey | 10 | $0.10 | $1.00 | https://www.digikey.com/en/products/detail/bourns-inc/CR0805-FX-1000ELF/3740946 | These resistors will be used with the status LEDs on the UAS.
ECH-U1H102JX5 (1nF Capacitor) | PCF1328CT-ND | Digikey | 4 | $0.48 | $1.92 | https://www.digikey.com/en/products/detail/panasonic-electronic-components/ECH-U1H102JX5/353701 | These capacitors will be used across the DC motors. This will lower the impedance and filter out voltage spikes from the changing output to the motors via a MOSFET and a microcontroller.
L196L-QBC (Blue SMD LED) | 2460-L196L-QBCTR-ND | Digikey | 10 | $0.26 | $2.60 | https://www.digikey.com/en/products/detail/american-opto-plus-led/L196L-QBC/12325436 | The LEDs will illuminate to allow the user to know when a node has a voltage applied to it. This will help the debugging if there are any issues within the UAS.
MECHANICAL PARTS:
M5x20mm Bolt, Nut, and Washer | 20mm | Amazon | 1 | 8.99 | 8.99 | https://www.amazon.com/Socket-Assortment-Stainless-Hexagonal-Washers/dp/B083DMQG1S?s=industrial | The nuts and bolts will be used to attach the 3D printed legs to the microcontroller.

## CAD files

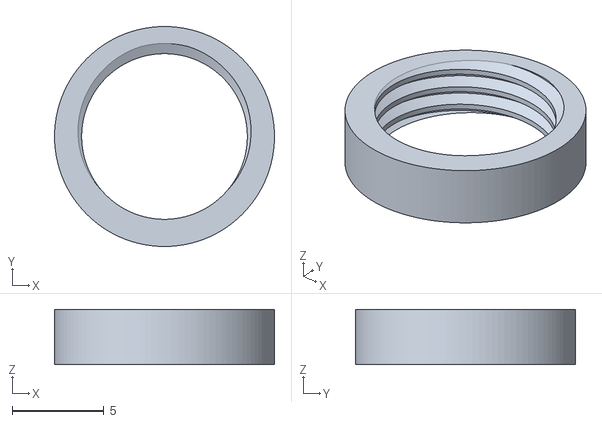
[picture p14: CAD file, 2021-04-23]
Fusion Parts/Motor Mounts/Nut.stl
12.0 x 12.0 x 3.00

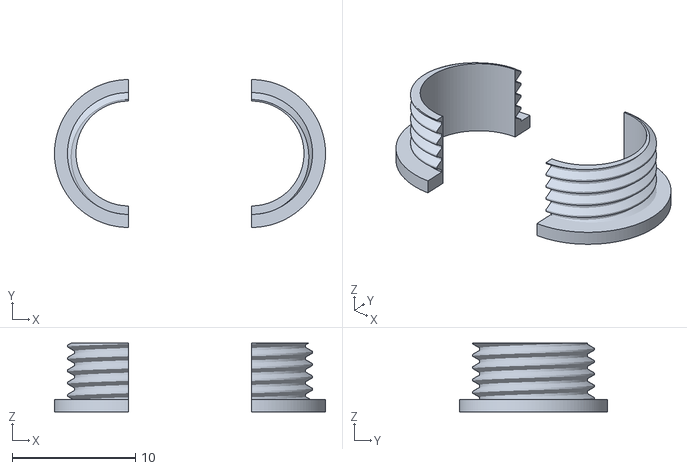
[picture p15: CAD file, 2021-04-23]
Fusion Parts/Motor Mounts/SplitBolt.stl
22.0 x 12.0 x 5.60

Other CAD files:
Fusion Parts/Brushed_UAS_PCB.f3d
Fusion Parts/UAS_Legs.f3d

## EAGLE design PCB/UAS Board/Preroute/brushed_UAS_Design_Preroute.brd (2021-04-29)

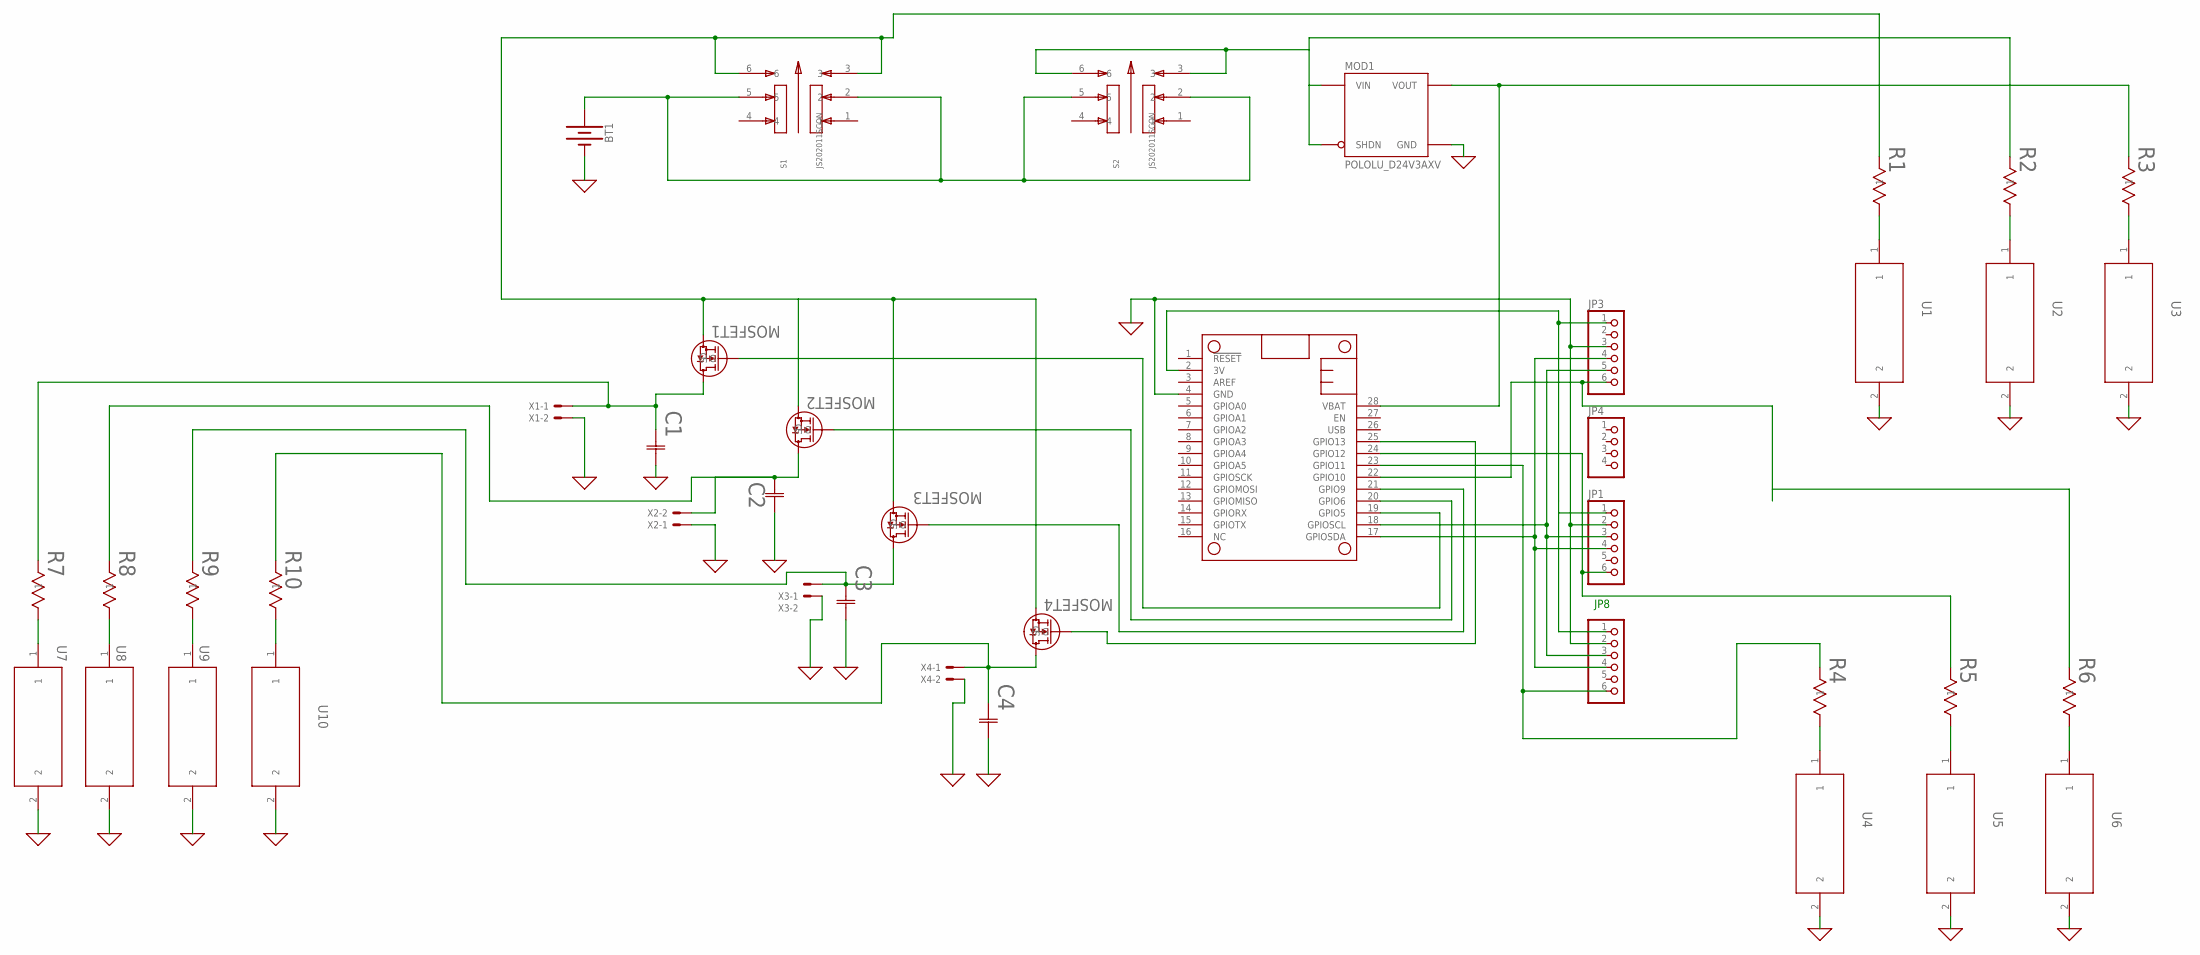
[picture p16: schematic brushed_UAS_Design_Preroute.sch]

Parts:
BT1: BATTERY-18650; BATTERY_18650-HOLDER
C1, C2, C3, C4: ECH-U1H102JX5CAP_J1_PAN-M; CAP_J1_PAN-M
JP1, JP8: HEADER-1X670MIL; 1X06_ROUND_70
JP3: HEADER-1X676MIL; 1X06_ROUND_76
JP4: HEADER-1X476MIL; 1X04_ROUND_76
MOD1: POLOLU_D24V3AXV; POLOLU_D24VXAYV_HC
MOSFET1, MOSFET2, MOSFET3, MOSFET4: SI2342DS-T1-GE3SOT-23_TO-236_VIS-M; SOT-23_TO-236_VIS-M
MS1: FEATHERWING_NODIM; FEATHERWING_DIM
R1, R2, R3, R4, R5, R6, R7, R8, R9, R10: CR0805-FX-1000ELFBO_CR0805-M; BO_CR0805-M
S1, S2: JS202011SCQN; SW_JS202011SCQN
U1, U2, U3, U4, U5, U6, U7, U8, U9, U10: L196L-QBCL196L-QBC_AOP-M; L196L-QBC_AOP-M
X1, X2, X3, X4: 22-23-2021

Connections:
0: BT1.GND@1 (-), C1.2, C2.2, C3.2, C4.2, JP1.2, JP3.3, JP8.2, MOD1.G (GND), MS1.4 (GND), U1.2, U2.2, U3.2, U4.2, U5.2, U6.2, U7.2, U8.2, U9.2, U10.2, X1.2, X2.1, X3.2, X4.2
3V: JP1.1, JP3.1, JP8.1, MS1.2 (3V)
unnamed: BT1.PWR@1 (+), S1.2, S1.5, S2.2, S2.5
unnamed: MOSFET1.2 (S), MOSFET2.2 (S), MOSFET3.2 (S), MOSFET4.2 (S), R1.1, S1.3, S1.6
unnamed: R1.2, U1.1
unnamed: R2.2, U2.1
unnamed: R3.2, U3.1
unnamed: MOD1.I (VIN), MOD1.S (SHDN), R2.1, S2.3, S2.6
unnamed: MOSFET1.1 (G), MS1.19 (GPIO5)
unnamed: MOSFET2.1 (G), MS1.20 (GPIO6)
unnamed: R4.2, U4.1
unnamed: R5.2, U5.1
unnamed: R6.2, U6.1
unnamed: MOSFET4.1 (G), MS1.25 (GPIO13)
unnamed: MOSFET3.1 (G), MS1.21 (GPIO9)
unnamed: JP1.4, JP3.4, JP8.4, MS1.17 (GPIOSDA)
unnamed: C4.1, MOSFET4.3 (D), R10.1, X4.1
unnamed: JP8.6, MS1.23 (GPIO11), R4.1
unnamed: R10.2, U10.1
unnamed: R9.2, U9.1
unnamed: R8.2, U8.1
unnamed: R7.2, U7.1
unnamed: JP1.3, JP3.5, JP8.3, MS1.18 (GPIOSCL)
unnamed: C3.1, MOSFET3.3 (D), R9.1, X3.1
unnamed: C1.1, MOSFET1.3 (D), R7.1, X1.1
unnamed: C2.1, MOSFET2.3 (D), R8.1, X2.2
unnamed: JP1.6, MS1.24 (GPIO12), R5.1
unnamed: JP3.6, MS1.22 (GPIO10), R6.1
VBAT: MOD1.O (VOUT), MS1.28 (VBAT), R3.1

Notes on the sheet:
JP8

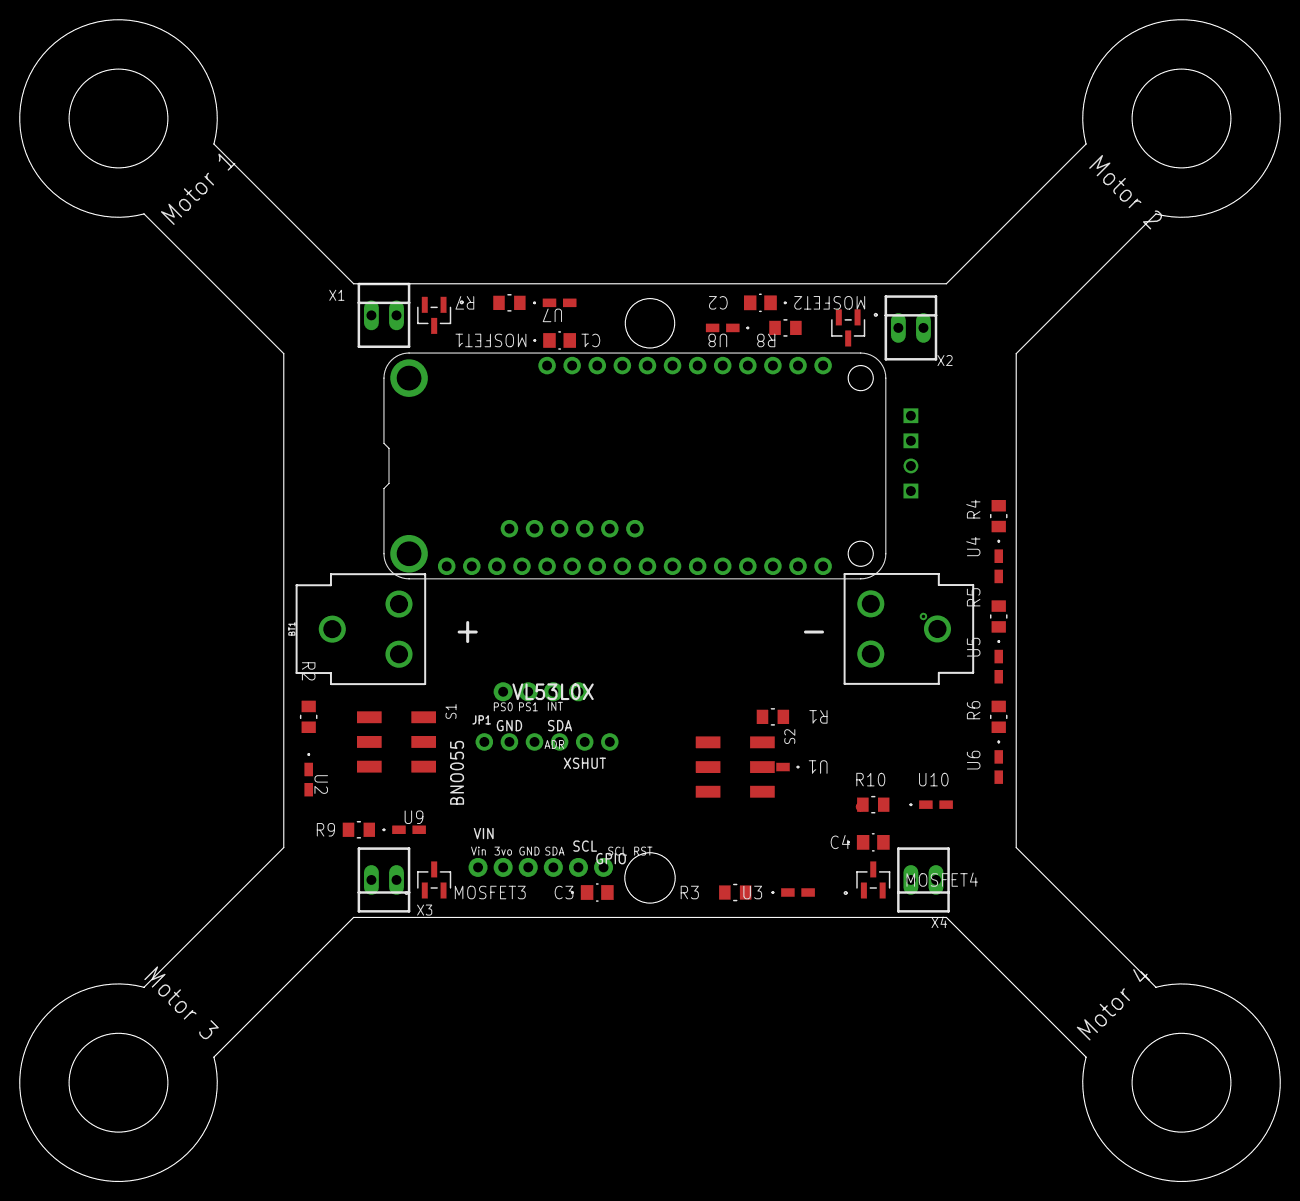
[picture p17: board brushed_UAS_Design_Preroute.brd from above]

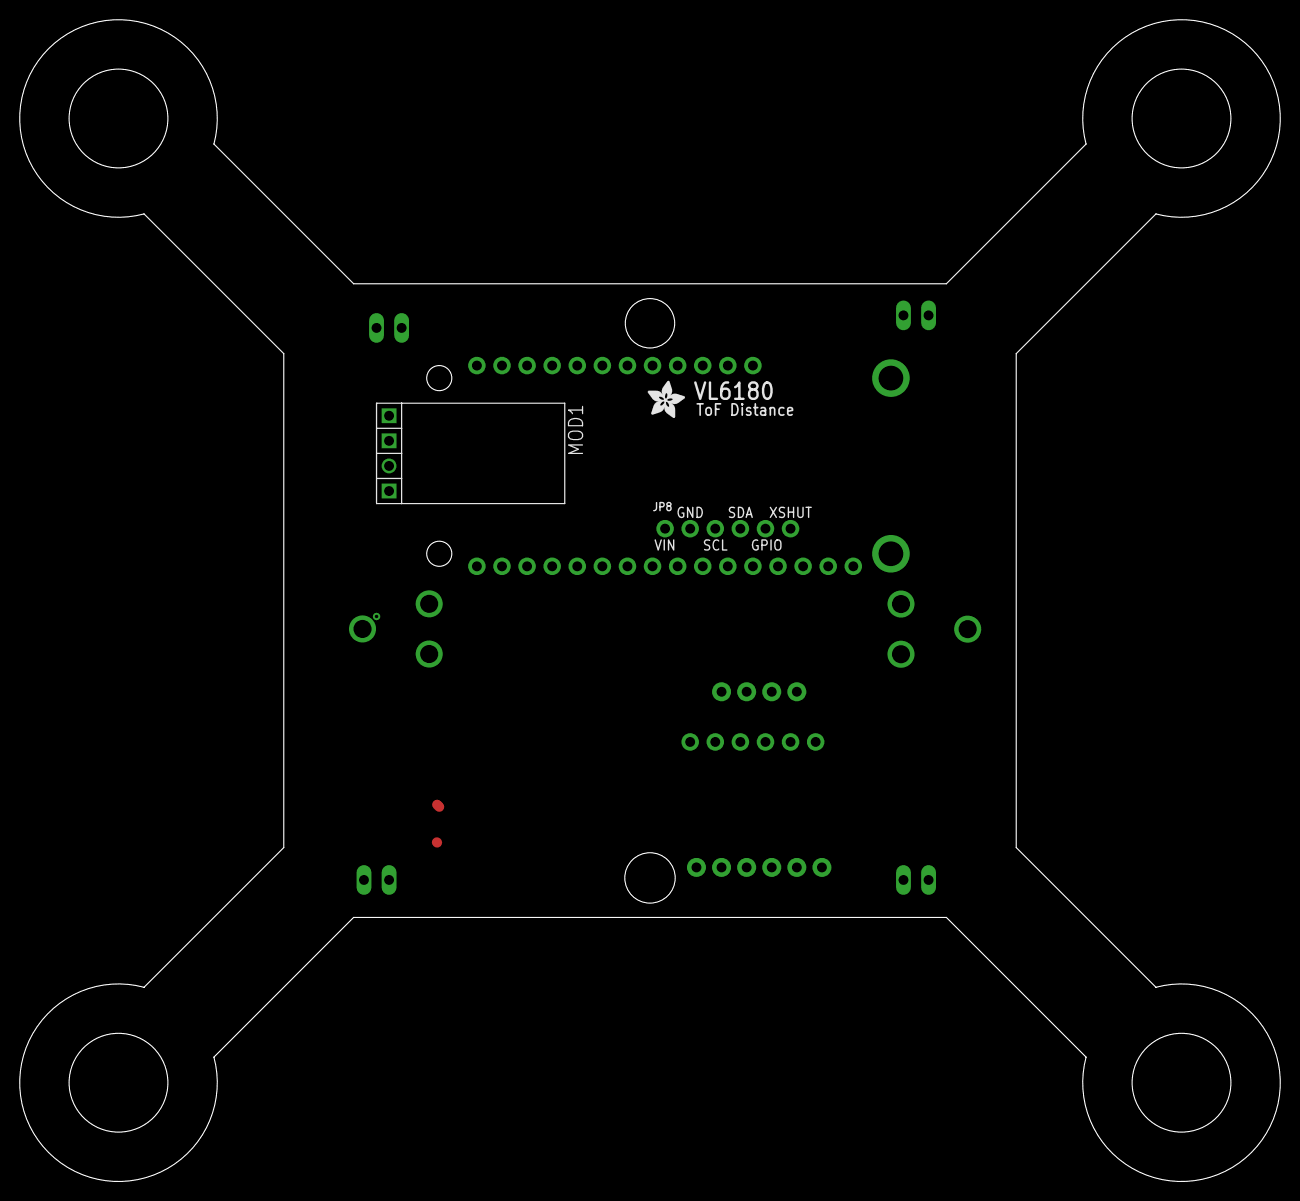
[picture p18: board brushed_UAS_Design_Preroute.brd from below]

Board: 2 copper layers, 127.6 x 117.6 mm, 42 parts (3 on the bottom side), 29 nets.

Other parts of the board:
U$19: ADAFRUIT_3.5MM

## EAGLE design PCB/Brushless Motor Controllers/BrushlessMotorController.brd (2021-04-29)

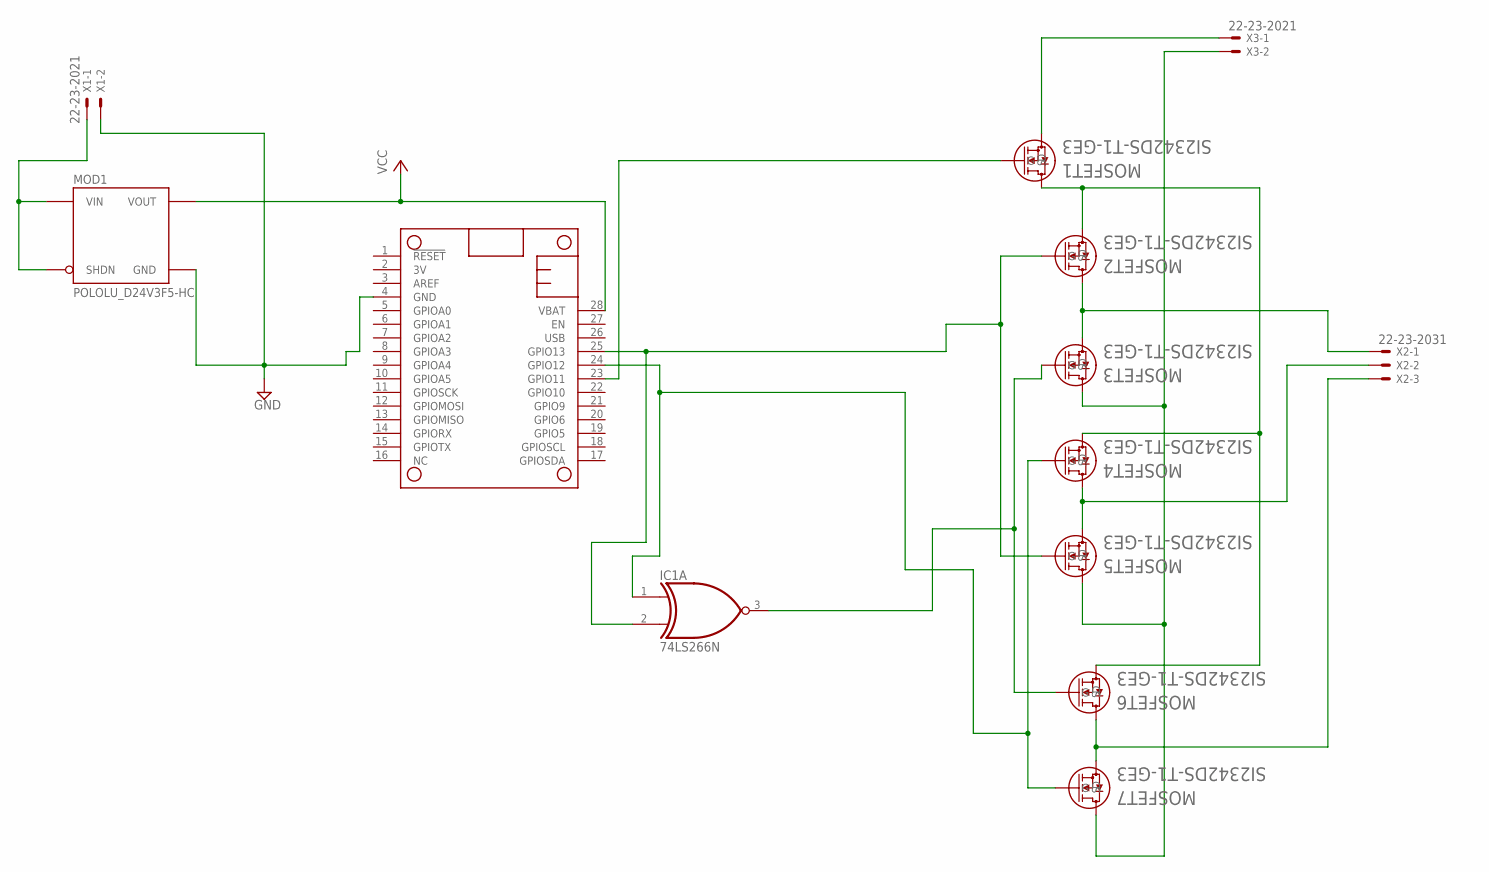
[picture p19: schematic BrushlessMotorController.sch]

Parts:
IC1: 74LS266N; DIL14
MOD1: POLOLU_D24V3F5-HC; POLOLU_D24V3F_HC
MOSFET1, MOSFET2, MOSFET3, MOSFET4, MOSFET5, MOSFET6, MOSFET7: SI2342DS-T1-GE3; SOT-23_TO-236_VIS
MS2: FEATHERWING_NODIM; FEATHERWING_DIM
X1, X3: 22-23-2021
X2: 22-23-2031

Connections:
GND: IC1.7 (GND), MOD1.G (GND), MS2.4 (GND), X1.2
unnamed: IC1.2 (I1), MOSFET2.1 (G), MOSFET5.1 (G), MS2.25 (GPIO13)
unnamed: IC1.1 (I0), MOSFET4.1 (G), MOSFET7.1 (G), MS2.24 (GPIO12)
unnamed: MOSFET1.2 (S), X3.1
unnamed: MOSFET1.1 (G), MS2.23 (GPIO11)
unnamed: MOD1.I (VIN), MOD1.S (SHDN), X1.1
unnamed: MOSFET3.3 (D), MOSFET5.3 (D), MOSFET7.3 (D), X3.2
unnamed: MOSFET1.3 (D), MOSFET2.2 (S), MOSFET4.2 (S), MOSFET6.2 (S)
unnamed: MOSFET2.3 (D), MOSFET3.2 (S), X2.1
unnamed: MOSFET4.3 (D), MOSFET5.2 (S), X2.2
unnamed: MOSFET6.3 (D), MOSFET7.2 (S), X2.3
unnamed: IC1.3 (O), MOSFET3.1 (G), MOSFET6.1 (G)
VCC: IC1.14 (VCC), MOD1.O (VOUT), MS2.28 (VBAT)

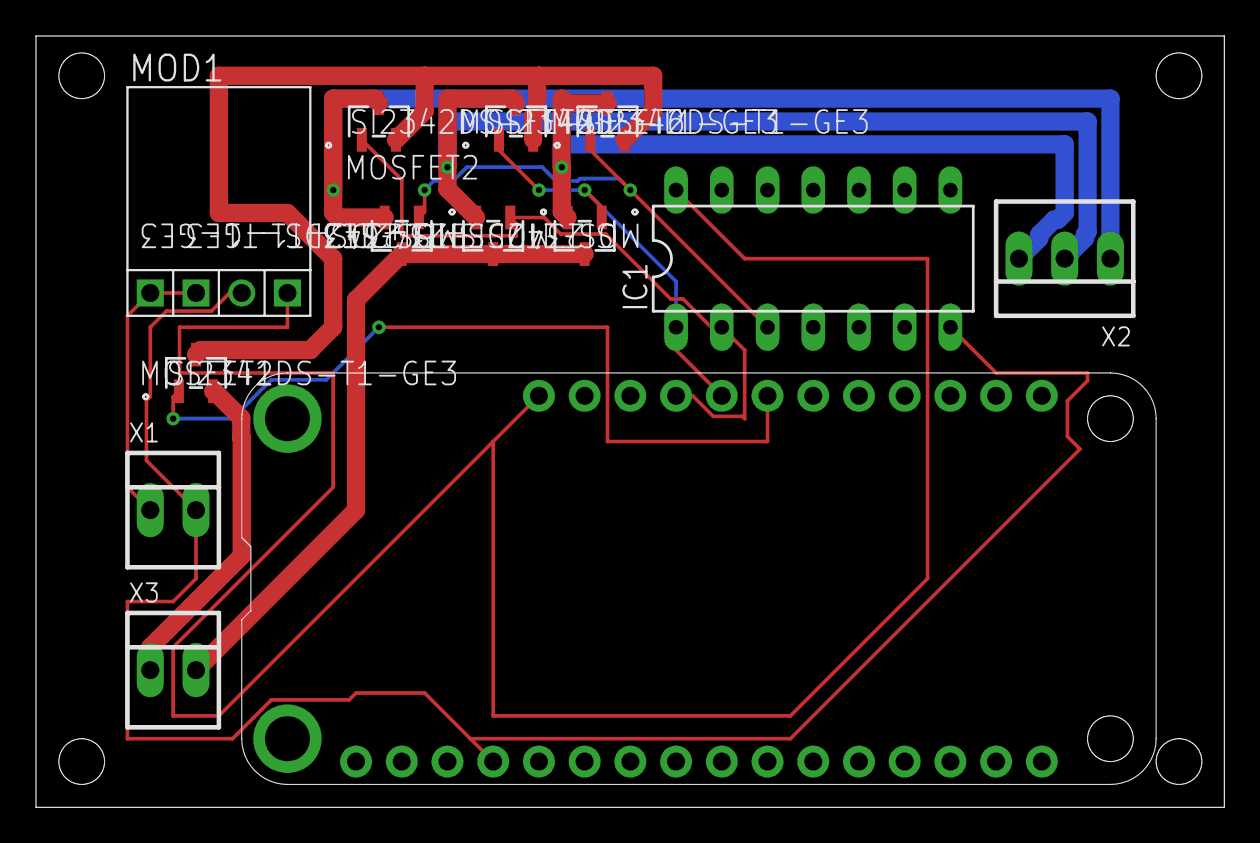
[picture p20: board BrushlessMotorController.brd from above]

Board: 2 copper layers, 66.0 x 42.9 mm, 13 parts (0 on the bottom side), 13 nets.

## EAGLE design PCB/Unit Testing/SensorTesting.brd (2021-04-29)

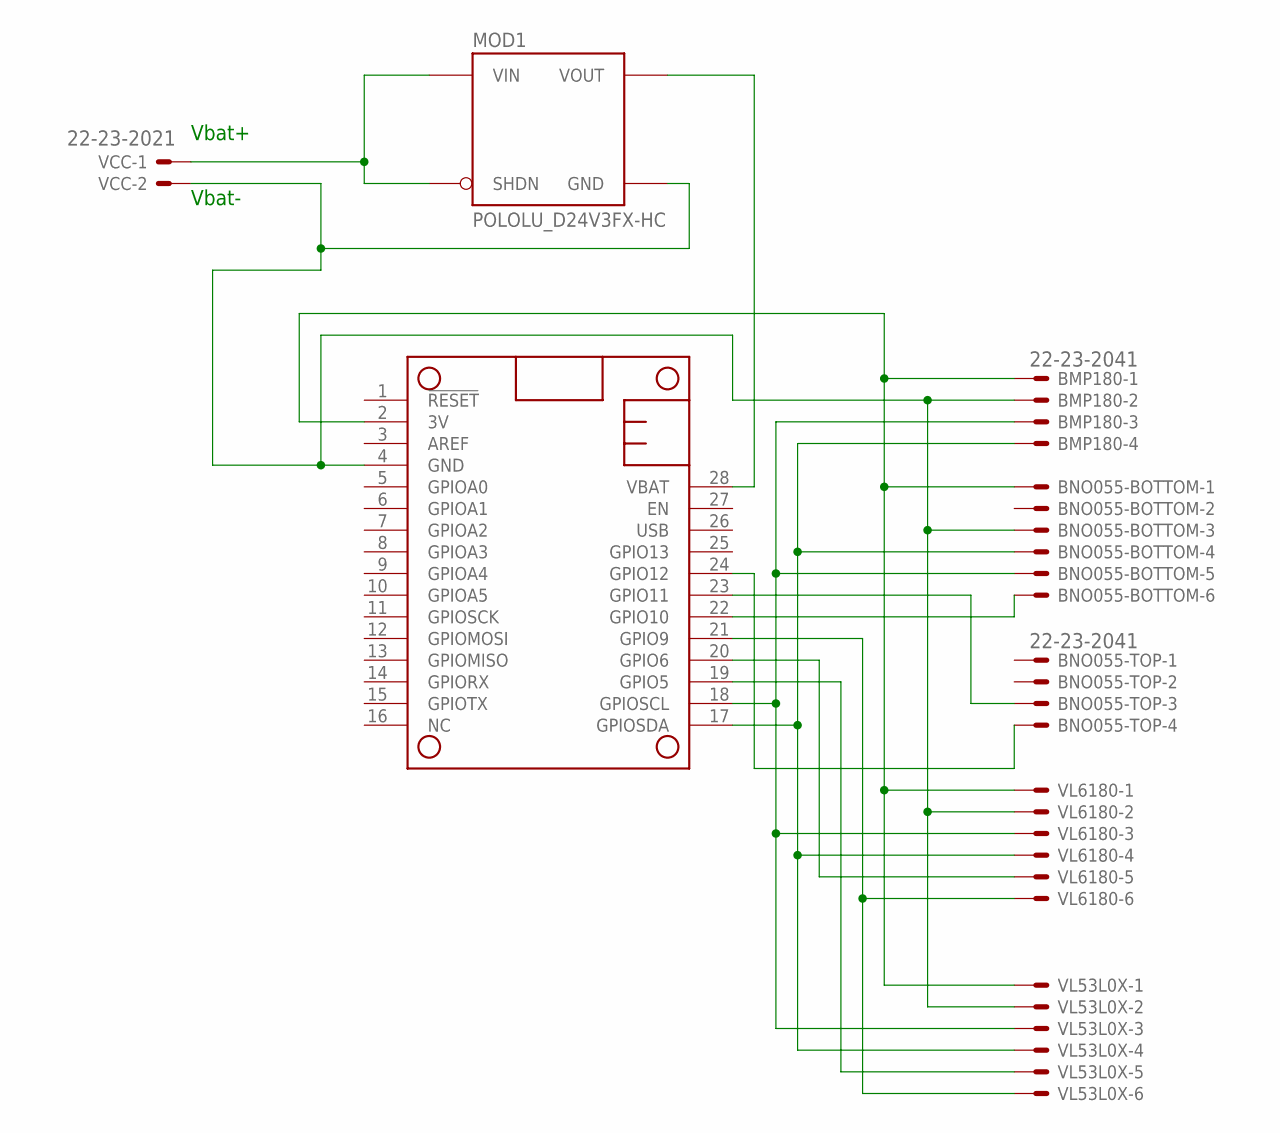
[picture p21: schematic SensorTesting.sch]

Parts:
BMP180: 22-23-2041
BNO055-BOTTOM: 22-23-2061
BNO055-TOP: 22-23-2041
MOD1: POLOLU_D24V3FX-HC; POLOLU_D24V3F_HC
MS1: FEATHERWING_NODIM; FEATHERWING_DIM
VCC: 22-23-2021
VL53L0X, VL6180: 22-23-2061

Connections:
3V: BMP180.1, BNO055-BOTTOM.1, MS1.2 (3V), VL53L0X.1, VL6180.1
unnamed: MS1.20 (GPIO6), VL6180.5
unnamed: BMP180.3, BNO055-BOTTOM.5, MS1.18 (GPIOSCL), VL53L0X.3, VL6180.3
unnamed: BMP180.4, BNO055-BOTTOM.4, MS1.17 (GPIOSDA), VL53L0X.4, VL6180.4
unnamed: BNO055-BOTTOM.6, MS1.22 (GPIO10)
unnamed: BNO055-TOP.3, MS1.23 (GPIO11)
unnamed: MS1.19 (GPIO5), VL53L0X.5
unnamed: MS1.21 (GPIO9), VL53L0X.6, VL6180.6
unnamed: BNO055-TOP.4, MS1.24 (GPIO12)
unnamed: MOD1.I (VIN), MOD1.S (SHDN), VCC.1
unnamed: BMP180.2, BNO055-BOTTOM.3, MOD1.G (GND), MS1.4 (GND), VCC.2, VL53L0X.2, VL6180.2
VBAT: MOD1.O (VOUT), MS1.28 (VBAT)

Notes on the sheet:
Vbat+
Vbat-

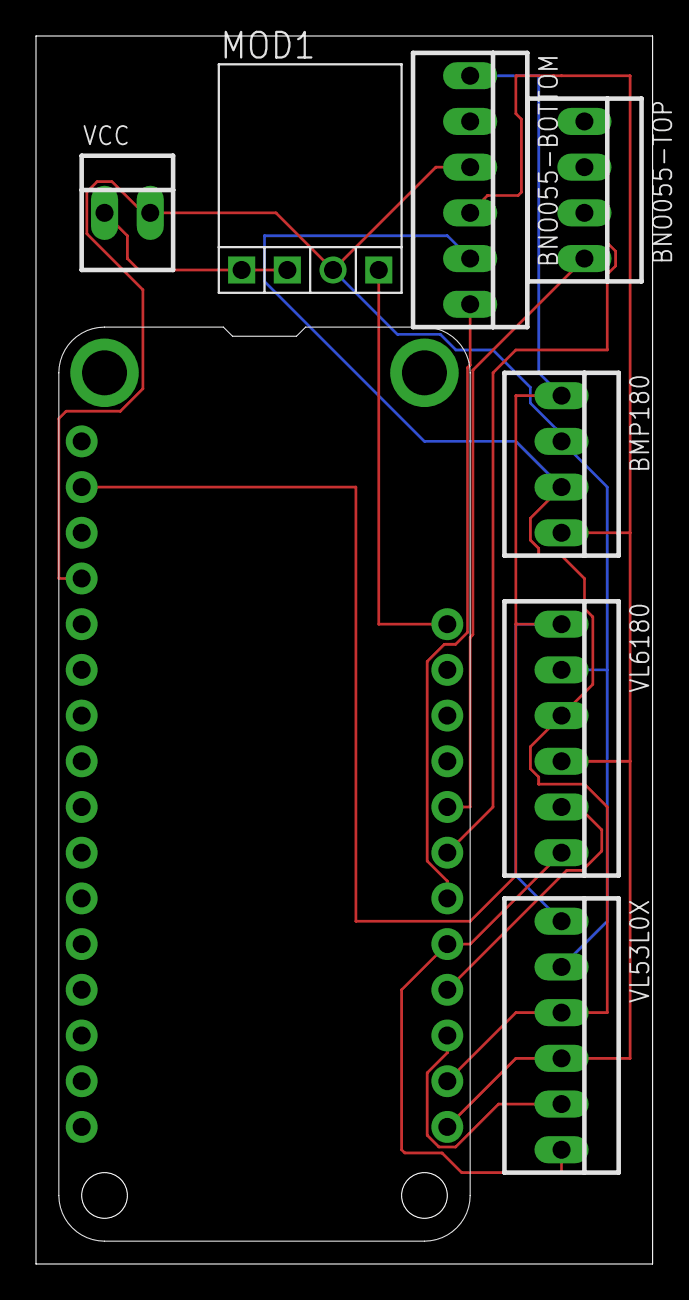
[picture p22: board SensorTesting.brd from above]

Board: 2 copper layers, 34.3 x 68.2 mm, 8 parts (0 on the bottom side), 12 nets.

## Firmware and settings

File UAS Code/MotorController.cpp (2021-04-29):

#include "Arduino.h"
#include "WildFlowerUAS.h"

// Define the pins for each motor.
#define MOTOR_BL A1
#define MOTOR_FL A2
#define MOTOR_FR A3
#define MOTOR_BR A4

// internal values
int motorSpeedBL;
int motorSpeedFL;
int motorSpeedFR;
int motorSpeedBR;

int BLCounter;
int FLCounter;
int FRCounter;
int BRCounter;

/* --- Constructor --- */
MotorController::MotorController(void)
{
  
}

/* Init Method */
int MotorController::Initialize(void)
{
  motorSpeedBL = 80;
  motorSpeedFL = 80;
  motorSpeedFR = 80;
  motorSpeedBR = 80;
  return 0;
}

float MotorController::StayAtHeight(float desiredHeight){
  sense.ReadCloseRangeLIDAR();
  sense.ReadLongRangeLIDAR();
  float closeL = Lidar.CloseRange;
  float longL = Lidar.LongRange;
  float currentHeight = longL;
  if (longL <= 100){ // Switch to the close range one - once we get down to mid range between the two's boundaries.
    currentHeight = closeL;
  }
  float error = desiredHeight - currentHeight; // positive when we need to go up, negative when we need to go down
  // For a velocity controller, we need:
  // desired velocity
  // actual velocity
  // way to set derivative of velocity (force)

}


/**
 * Takes a force that we want from each motor (in pounds/newtons) and converts it into something that the MCU
 * can read and use to switch the motors periodically (a floating percentage.)
 * If a upwards or downwards force greater than we can give is requested, set it to the max in that direction
 * and send a message to the serial communications line.
 */
int MotorController::SetMotorForces(float BL_Force, float FL_Force, float FR_Force, float BR_Force){
  float maxThrust = 10; // say its like 10 lbs
  float droneWeight = 8; // 8 lbs
  // The maximum force it can have upwards is maxThrust - droneWeight.
  // The maximum force it can have going downwards is droneWeight (our rotors don't spin backwards.)
  // The difference between these two is maxThrust.
  // In this case, 0% of maxThrust would be -8 lbs of force, 100% of maxThrust would be +2 lbs of force.
  // 
  // (-8 + 8) / 10 * 100 = 0
  // (-2 + 8) / 10 * 100 = 60
  // (0  + 8) / 10 * 100 = 80
  // (2  + 8) / 10 * 100 = 100


  // Init the percent of time each motor should be driven high.  
  float percentBL = (BL_Force + droneWeight/4) / maxThrust * 100;
  if (percentBL > 100) {
    percentBL = 100;
    Serial.print("Trying to get more force than we can muster out of motor BL!");
  }
  else if (percentBL < 0){
    percentBL = 0;
    Serial.print("Trying to drop faster than gravity will allow for side BL!");
  }

  float percentFL = (FL_Force + droneWeight/4) / maxThrust * 100;
  if (percentFL > 100) {
    percentFL = 100;
    Serial.print("Trying to get more force than we can muster out of motor FL!");
  }
  else if (percentFL < 0){
    percentFL = 0;
    Serial.print("Trying to drop faster than gravity will allow for side FL!");
  }

  float percentFR = (FR_Force + droneWeight/4) / maxThrust * 100;
  if (percentFR > 100) {
    percentFR = 100;
    Serial.print("Trying to get more force than we can muster out of motor FR!");
  }
  else if (percentFR < 0){
    percentFR = 0;
    Serial.print("Trying to drop faster than gravity will allow for side FR!");
  }
  
  float percentBR = (BR_Force + droneWeight/4) / maxThrust * 100;
  if (percentBR > 100) {
    percentBR = 100;
    Serial.print("Trying to get more force than we can muster out of motor BR!");
  }
  else if (percentBR < 0){
    percentBR = 0;
    Serial.print("Trying to drop faster than gravity will allow for side BR!");
  }
  
}

// Function that should be called in main to spin the motors in a time-sensitive manner.
int MotorController::SpinMotors(void)
{
  if (BLCounter > motorSpeedBL) digitalWrite(MOTOR_BL, LOW); // turn off for (100-BL)% of the time.
  else digitalWrite(MOTOR_BL, HIGH); // turn on for BL% of the time.
  if (FLCounter > motorSpeedFL) digitalWrite(MOTOR_FL, LOW);
  else digitalWrite(MOTOR_FL, HIGH);
  if (FRCounter > motorSpeedFR) digitalWrite(MOTOR_FR, LOW);
  else digitalWrite(MOTOR_FR, HIGH);
  if (BRCounter > BRCounter) digitalWrite(MOTOR_BR, LOW);
  else digitalWrite(MOTOR_BR, HIGH);
  
  BLCounter++;
  FLCounter++;
  FRCounter++;
  BRCounter++;
  
  // When counters reach > 100, set back to 0.
  if (BLCounter > 100) BLCounter = 0;
  if (FLCounter > 100) FLCounter = 0;
  if (FRCounter > 100) FRCounter = 0;
  if (BRCounter > 100) BRCounter = 0;
  return 0;
}

int setYaw()
{
  
}

int setRoll()
{
  
}

int setPitch()
{
  
}

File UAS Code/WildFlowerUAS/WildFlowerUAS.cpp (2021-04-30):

//************************************************************************************************
//-------------------------------------Header Files-----------------------------------------------
//************************************************************************************************

#include "Arduino.h"
#include "WildFlowerUAS.h"

//************************************************************************************************
//---------------------------------------Define Constants-----------------------------------------
//************************************************************************************************

/*--I2C addresses--*/
#define VL53L0X_ADR 0x30                //newly assigned I2C address for Long-Range LIDAR
#define VL6180X_ADR 0x29                //Standard I2C address for Short-Range LIDAR
#define BNO055_ADR 0x28                 //IMU Standard address

/*--SHUTDOWN PINS--*/
#define IMU_XSHUT 10                                //pin to reset IMU
#define VL6180X_XSHUT 11                            //pin to reset Short-Range LIDAR

//*************************************************************************************************
//---------------------------------Initialize Class Instances--------------------------------------
//*************************************************************************************************

/*--Sensors--*/
Adafruit_VL53L0X LR = Adafruit_VL53L0X();           //class for Long-Range LIDAR
Adafruit_VL6180X CR = Adafruit_VL6180X();           //class for Close-Range LIDAR
Adafruit_BNO055 bno = Adafruit_BNO055(55, 0x28);    //class for IMU


//*************************************************************************************************
//---------------------------------Initialize Global Variables-------------------------------------
//*************************************************************************************************

VL53L0X_RangingMeasurementData_t LongRangeLIDARData;      //Long-Range LIDAR data object
int LR_Lidar_Address = 0x29; 

//*************************************************************************************************
//---------------------------------Global Structure Initializations--------------------------------
//*************************************************************************************************

struct TxStruct TxData;
struct TxStruct RxData;
struct LidarStruct Lidar;

//*************************************************************************************************
//-----------------------------------------SENSORS CLASS-------------------------------------------
//*************************************************************************************************

//*************************************************************************************************
//-------------------------------------SENSORS PUBLIC METHODS--------------------------------------
//*************************************************************************************************

/*------------------------------SENSORS Constructor Method-------------------------------*/
SENSORS::SENSORS(void)
{

}

/*------------------------------SENSORS Initialize Method-------------------------------*/
int SENSORS::Initialize(void)
{

  Serial.begin(9600);
  
  //begin communication through I2C
  Wire.begin();
    
  //Setup the I2C addresses and VL53L0X
  SENSORS::SetupI2CAddresses();

  //Setup the other two sensors
  SENSORS::SetupSensors();

  return 1;
}

/*------------------------------Read IMU Data Method-------------------------------*/
void SENSORS::ReadIMU(void)
{
    //measure from IMU
    //could add VECTOR_ACCELEROMETER, VECTOR_MAGNETOMETER,VECTOR_GRAVITY...

    //create sensor events from adafruit driver
    sensors_event_t orientation , angularVelocity , linearAcceleration, magnetometer, accelerometer, gravity;

    //record the data values from the sensor
    bno.getEvent(&orientation, Adafruit_BNO055::VECTOR_EULER);                //orientation
    bno.getEvent(&angularVelocity, Adafruit_BNO055::VECTOR_GYROSCOPE);        //angular velocity
    bno.getEvent(&linearAcceleration, Adafruit_BNO055::VECTOR_LINEARACCEL);   //;omear acceleration
    bno.getEvent(&magnetometer, Adafruit_BNO055::VECTOR_MAGNETOMETER);        //linear magnetometer data
    bno.getEvent(&accelerometer, Adafruit_BNO055::VECTOR_ACCELEROMETER);      //linear accelerometer data
    bno.getEvent(&gravity, Adafruit_BNO055::VECTOR_GRAVITY);                  //linear gravity (from accelerometer)

    //print the results through the previously written UDF
    SENSORS::printEvent(&orientation);
    SENSORS::printEvent(&angularVelocity);
    SENSORS::printEvent(&linearAcceleration);
    SENSORS::printEvent(&magnetometer);
    SENSORS::printEvent(&accelerometer);
    SENSORS::printEvent(&gravity);

    //read values to the structure
    TxData.Position.x = (double)orientation.orientation.x;
    TxData.Position.y = (double)orientation.orientation.y;
    TxData.Position.z = (double)orientation.orientation.z;

    TxData.Rotation.x = (double)angularVelocity.gyro.x;
    TxData.Rotation.y = (double)angularVelocity.gyro.y;
    TxData.Rotation.z = (double)angularVelocity.gyro.z;

    //TxData.Mode = (uint16_t)1;

    //get board temperature as well
    int8_t boardTemp = bno.getTemp();

    //print temperature
    Serial.print(F("temperature: "));
    Serial.println(boardTemp);

    //create unsigned byte integer values 
    uint8_t system, gyro, accel, mag = 0;

    //get calibration data
    bno.getCalibration(&system, &gyro, &accel, &mag);

    //print the calibration data to the user
    Serial.print("Calibration: Sys=");
    Serial.print(system);
    Serial.print(" Gyro=");
    Serial.print(gyro);
    Serial.print(" Accel=");
    Serial.print(accel);
    Serial.print(" Mag=");
    Serial.println(mag);
}
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

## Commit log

2021-04-23 Current Versioning
    This consists of all the current software and other files used within our Wildflower UAS.
    [4-20-2021 8-47-36 PM--TX.xlsx, 4-20-2021 8-47-47 PM--RX.xlsx, 4-20-2021 8-47-53 PM--TX-and-RX.xlsx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]
2021-04-29 Repo Organization
    [4-20-2021 8-47-36 PM--TX.xlsx, 4-20-2021 8-47-47 PM--RX.xlsx, 4-20-2021 8-47-53 PM--TX-and-RX.xlsx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]
2021-04-29 Updated Repo Contents
    Added the parts list as well as an image was renamed.
    [BrushedPartsList.xlsx]
2021-04-29 Updated LabVIEW Files
    [4-20-2021 8-47-36 PM--TX.xlsx, 4-20-2021 8-47-47 PM--RX.xlsx, 4-20-2021 8-47-53 PM--TX-and-RX.xlsx]
2021-04-29 merged class in from MotorController.cpp
2021-04-29 Update WildFlowerUAS.h
    merged header files from MotorController.h
2021-04-29 Bang-bang controller and PID in SetUASOrientation()
2021-04-29 Added appropriate function prototypes for MC
2021-04-29 Added a unit test for testing roll functionality.
    Wobble_Test will periodically swap between a user-specified positive rolling angle, negative version of that angle, and neutral position.
    [Wobble_Test.ino]
2021-05-02 Changed Schematic Dimensions

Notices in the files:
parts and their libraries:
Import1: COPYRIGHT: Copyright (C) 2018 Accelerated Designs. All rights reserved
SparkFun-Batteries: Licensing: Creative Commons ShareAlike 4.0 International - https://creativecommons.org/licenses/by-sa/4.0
